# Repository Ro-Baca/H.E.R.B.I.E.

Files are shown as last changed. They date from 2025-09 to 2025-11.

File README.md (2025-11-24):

# **H.E.R.B.I.E.** <br> <span style="font-size:60%;">**H**orticultural **E**lectronic **R**obot **B**udy **I**nteractive **E**ntity</span>

> ![Logo de H.E.R.B.I.E. o la foto del robot]

 

H.E.R.B.I.E. es un prototipo de robot social de código abierto, diseñado para ser una plataforma de investigación accesible en el campo de la Interacción Humano-Robot (HRI). Fue desarrollado siguiendo una metodología de Ingeniería de Sistemas para estudiar cómo la filosofía de 'Robot Débil' puede fomentar la cooperación y el acoplamiento social con los usuarios.

## Modelo


### Conceptual
Define los **actores y requerimientos de usuario** (el "Qué" y "Por qué" del sistema). 

 

### Lógico
Describe la **estructura funcional** y las interacciones del sistema, agnósticas a la tecnología.

 

### Tecnológico
Define la **arquitectura concreta**, componentes de hardware y plataformas de software específicas.

 

## Hardware
Esta sección contiene los planos de los componentes y su interconexión, esenciales para la replicabilidad.
### Circuitos
Aquí se encuentran los diagramas eléctricos y pinouts para la interconexión de sensores y actuadores.

### CAD
Archivos STL para los encapsulamientos modulares, diseñados para impresión FDM en PLA.

## Software
El software se divide en una arquitectura dual:

### Cerebro (Raspberry Pi Zero)
-   **Función:** Procesamiento de alto nivel, servidor web y base de datos.
-   **Tecnologías:** Python, Flask, SQLite.

### Controlador (Raspberry Pi Pico)
-   **Función:** Gestión de entradas/salidas (lectura de sensores y control de actuadores) en tiempo real.
-   **Tecnologías:** MicroPython.

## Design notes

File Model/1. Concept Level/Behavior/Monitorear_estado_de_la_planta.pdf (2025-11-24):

uc [package] Behavior [Monitorear estado de la planta]

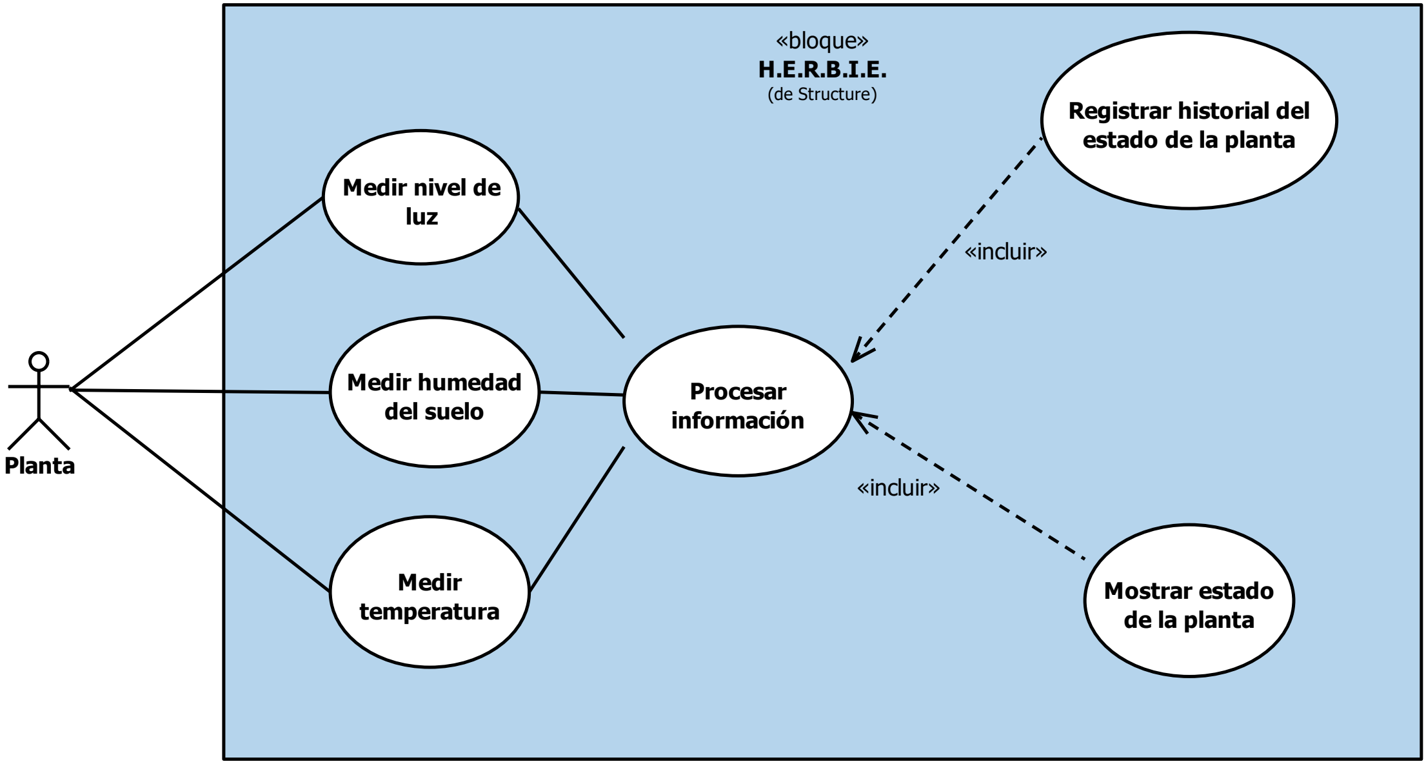
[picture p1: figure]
Planta; «bloque» H.E.R.B.I.E. (de Structure); Medir temperatura; Medir humedad del suelo; Medir nivel de luz; Procesar información; Mostrar estado de la planta; Registrar historial del estado de la planta; «incluir»

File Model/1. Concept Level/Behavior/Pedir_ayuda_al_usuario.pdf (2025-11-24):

uc [package] Behavior [Pedir ayuda al usuario]

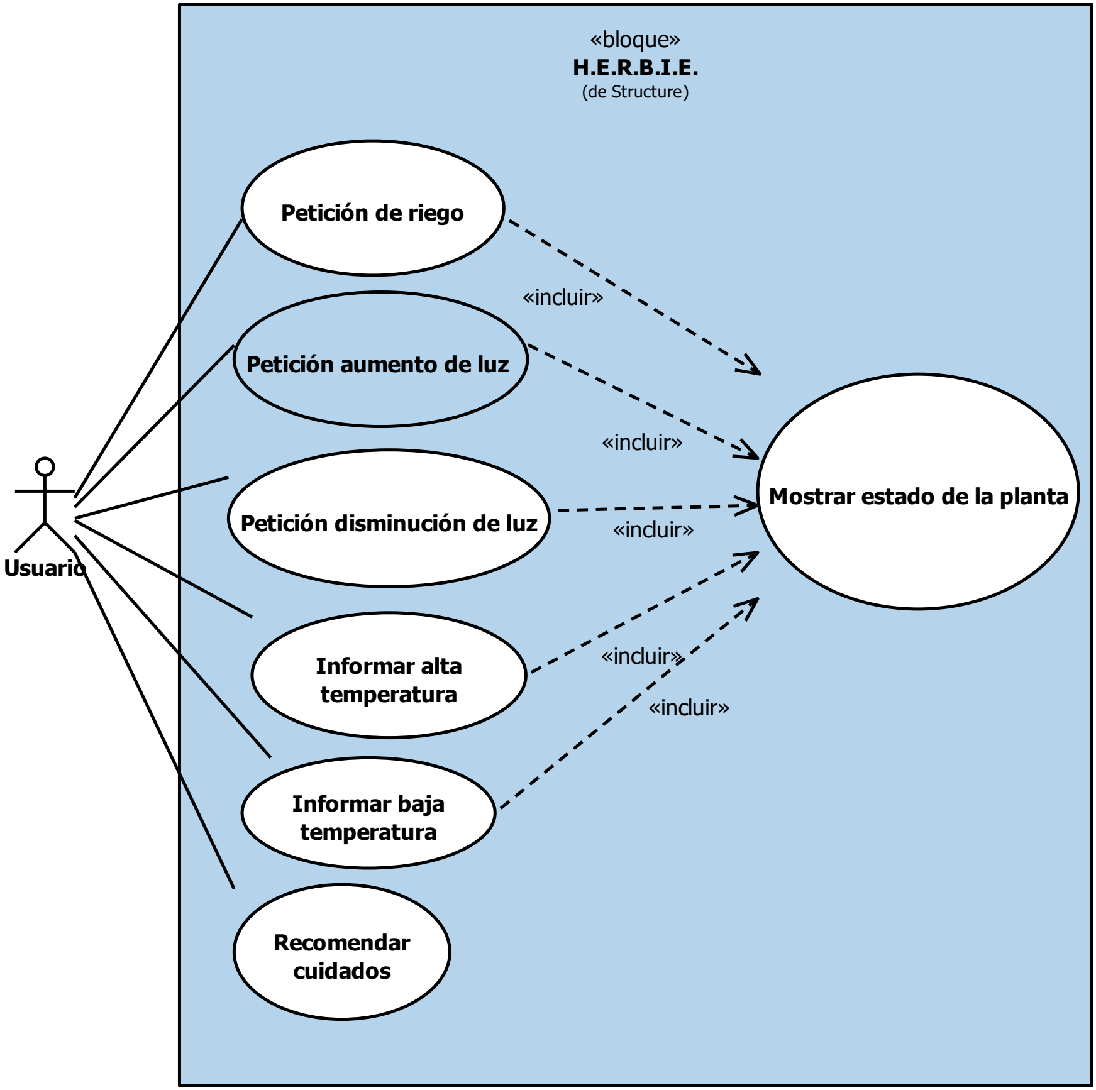
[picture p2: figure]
Usuario; «bloque» H.E.R.B.I.E. (de Structure); Petición aumento de luz; Petición de riego; Petición disminución de luz; Recomendar cuidados; Informar alta temperatura; Informar baja temperatura; Mostrar estado de la planta; «incluir»

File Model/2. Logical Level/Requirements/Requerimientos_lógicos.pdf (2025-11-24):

«requisito»
Sensor de temperatura
Id: LR-01
Text: El sistema debe de
contener un sensor capaz de medir la temperatura del
ambiente.

«requisito»
Sensor de humedad
Id: LR-02
Text: El sistema debe contener un sensor capaz de medir la humedad del suelo de la
planta.

«requisito»
Sensor de luz
Id: LR-03
Text: El sistema debe contener un sensor capaz de medir el nivel de luz que incide en la planta.

«requisito»
Controlador del sistema
Id: LR-04
Text: El sistema debe contener un elemento capaz de procesar la informacion de los sensores.

«requisito»
Sensado de temperatura
Id: LR-08
Text: El sistema deberá medir periódicamente la temperatura del ambiente utilizando el sensor de temperatura.

«requisito»
Sensado de humedad
Id: LR-09
Text: El sistema deberá medir periódicamente la humedad del suelo de la planta utilizando el sensor de humedad.

«requisito»
Sensado de nivel luz
Id: LR-10
Text: El sistema deberá medir periódicamente el nivel de luz que incide en la planta utilizando el sensor de luz.

«requisito»
Actuador de sonido
Id: LR-05
Text: El sistema debe contener un actuador para efectuar
acciones de sonido.

«requisito»
Actuador de luz
Id: LR-06
Text: El sistema debe contener un actuador para efectuar acciones de luz.

«requisito»
Interfaz de Usuario Gráfico Id: LR-07
Text: El sistema debe de
proveer una Interfaz Grafica de Usuario para interactuar con el usuario.

«requisito»
Base de datos Interna
Id: LR-13
Text: El sistema debe almacenar la informacion de los sensores localmente en una base de datos interna.

«requisito»
Señal de temperatura
Id: LR-20
Text: El sensor de temperatura debe mandar la señal de temperatura al controlador con el itemFlow Sens_data.

«requisito»
Señal de humedad
Id: LR-21
Text: El sensor de humedad debe mandar la señal de humedad al controlador con el itemFlow Sens_data.

«requisito»
Señal de luz
Id: LR-22
Text: El sensor de luz debe mandar la señal de nivel de luz con el itemFlow Sens_data.

«requisito»
Configuracion volumen del
actuador
Id: LR-16
Text: El sistema debe permitir al usuario configurar el volumen del actuador sonoro.

«requisito»
Configuración brillo del
actuador
Id: LR-17
Text: El sistema debe permitir al usuario configurar el brillo del actuador de luz.

«requisito»
Configuración frecuencia de medición
Id: LR-18
Text: El sistema debe de permitir al usuario configurar la frecuencia de medicion de los sensores.

«requisito»
Configuracion de umbral de Temperatura
Id: LR-11
Text: El sistema debe permitir al usuario configurar el valor de umbral de temperatura.

«requisito»
Configuración de umbral de humedad
Id: LR-15
Text: El sistema debe permitir al usuario configurar el valor de umbral de humedad.

«requisito»
Configuración de umral de nivel de luz
Id: LR-19
Text: El sistema debe permitir al usuario configurar el valor de umbral de nivel de luz.

«requisito»
Controlador de datos del
sensor
Id: LR-12
Text: El controllador debe recibir la información de los sensores para procesarla.

«requisito»
Mostrar información de planta Id: LR-14
Text: El controlador debe mandar la informacion del estado de la planta a la IUG.

«requisito»
Valores de configuracion del controlador.
Id: LR-23
Text: El controlador debe recibir el itemFlow config_values cuando un nuevo valor de configuracion es requerido.

«requisito»
Mostrar valores de
configuración
Id: LR-28
Text: La IUG debe mandar el itemFlow config_values al
controlador cuando se establece un nuevo valor.

«requisito»
Solicitud de actuación de
controlador
Id: LR-24
Text: El controlador debe mandar el itemFlow Act_com para solicitar una acción de los actuadores.

«requisito»
Función de procesamiento de sensor
Id: LR-26
Text: El controlador debe recibir el itemFlow sens_data, procesar la información y mandar la señal mes_values.

«requisito»
Función calcular estatus planta Id: LR-27
Text: El controlador debe recibír los intemFlow mes_values y
config_values para calcular el estado de la planta.

«requisito»
Mostrar informacion gráfica de planta
Id: LR-25
Text: La IGU debe recibír los intemFlow sens_data y plnt_stat para mostrar la información al usuario.

«requisito»
Función calcular emocion del robot Id: LR-29
Text: El controlador debe recibír el itemFlow plnt_stat para calcular la emoción del robot y mandar las señales son_com y lig_com.

«requisito»
Temperatura ok
Id: LR-31
Text: Cuando el itemFlow temp_sensor_data < max_temp y temp_sensor_data> min_temp, el controlador debe establecer temp_stat = ok.

«requisito»
Humedad ok
Id: LR-34
Text: Cuando el itemFlow moist_sensor_data < max_moist y moist_sensor_data > min_moist, el controlador debe establecer moist_stat = ok.

«requisito»
Luz ok
Id: LR-38
Text: Cuando light_sensor_data < max_light AND light_sensor_data > min_light, el controlador debe establacer temp_stat = ok.

«requisito»
Temperatura Alta
Id: LR-32
Text: Cuando el itemFlow temp_sensor_data >max_temp, el controlador debe establecer temp_stat = high.

«requisito»
Humedad alta
Id: LR-35
Text: Cuando moist_sensor_data > max_moist, el controlador debe establecer moist_stat = high.

«requisito»
Luz alta
Id: LR-39
Text: Cuando light_sensor_data > max_light, el controlador debe establecer light_stat = high.

«requisito»
Temperatura baja
Id: LR-33
Text: Cuando el itemFlow temp_sensor_data < min_temp, el controlador debe establecer temp_stat = low.

«requisito»
Humedad baja
Id: LR-36
Text: Cuando moist_sensor_data < min_moist, el controlador debe establecer moist_stat = low.

«requisito»
Luz baja
Id: LR-40
Text: Cuando light_sensor_data < max_light, el controlador debe establecer light_stat = low.

«requisito»
Estructura plnt_stat
Id: LR-30
Text: El itemFlow plnt_stat debe estar compuesto de tres variables: temp_stat, moist_stat y light_stat.

«requisito»
Estructura emocion del robot Id: LR-44
Text: El itemFlow robot_emo debe estar compuesto por tres variables: temp_emo, moist_emo, light_emo.

«requisito»
Emocion temperatura ok
Id: LR-45
Text: Cuando temp_stat == ok, el controlard debe establecer temp_emo = ok.

«requisito»
Emoción humedad ok
Id: LR-48
Text: Cuando moist_stat == ok, el controlador deber establecer moist_emo = ok.

«requisito»
Emoción luz ok
Id: LR-51
Text: Cuando light_stat == ok, el controlador deber establecer light_emo = ok.

«requisito»
Emoción temperatura caliente Id: LR-46
Text: Cuando temp_stat == high, el controlador debe establecer temp_emo = hot.

«requisito»
Emoción humedad seco
Id: LR-49
Text: Cuando moist_stat == low, el controlador deber establecer moist_emo = dry.

«requisito»
Sin humedad
Id: LR-37
Text: Cuando
moist_sensor_data == 0, el controlador debe establecer moist_stat = dead.

«requisito»
Emoción luz cansado
Id: LR-52
Text: Cuando light_stat == high, el controlador debe establecer light_emo = tired.

«requisito»
Emoción temperatura fría
Id: LR-47
Text: Cuando temp_stat == low, el controlador debe establecer temp_emo = cold.

«requisito»
Emoción humedad muerto
Id: LR-50
Text: Cuando moist_stat == dead, el controlador deber establecer moist_emo = dead.

«requisito»
Emoción luz triste
Id: LR-53
Text: Cuando light_stat == low, el controlador debe establecer light_emo = tired.

«requisito»
Comando emoción muesto
Id: LR-56
Text: Cuando mosit_emo == dead, el controlador debe establecer led_command = [red,still,fast] y sound_command = [0,0].

«requisito»
Estructura comando luz
Id: LR-54
Text: El itemFlow led_command debe estar compuesto de tres variables: color, modeo, velocidad.

«requisito»
Estructura comando sonido
Id: LR-55
Text: El itemFlow sound_command debe estar compuesto de dos variables: tono y velocidad.

«requisito»
Comando emoción seco
Id: LR-57
Text: Cuando mosit_emo == dry, el controlador debe establcer led_command = [blue,blink,fast] y sound_command = [1,-1].

«requisito»
Comando emoción frío
Id: LR-59
Text: Cuando temp_emo == cold y moist_emo == ok, el controlador debe establecer led_command = [blue,still,fast] y sound_command = [1,1].

«requisito»
Comando emoción triste
Id: LR-60
Text: Cuando light_emo == sad y temp_emo == ok y moist_emo == ok, el controlador debe establecer led_command = [blue,blink,slow] y sound_command = [-1,-1].

«requisito»
Comando emoción caliente
Id: LR-58
Text: Cuando temp_emo == hot y moist_emo == ok, el controlador debe establecer led_command = [red,blink,fast] y sound_command = [1,1].

«requisito»
Comando emoción cansado
Id: LR-61
Text: Cuando light_emo == tired y temp_emo == ok y moist_emo == ok, el controlador debe establecer led_command = [green,blink,fast] y sound_command = [-1,-1].

«requisito»
Comando emoción feliz
Id: LR-62
Text: Cuando light_emo == ok y temp_emo == ok y moist_emo == ok, el controlador debe establecer led_command = [green,still,fast] y sound_command = [0,0].
Estructura | Funcionalidad
DataFlow | Estado de la planta

Emociones
del robot

Comandos
de actuación

«requisito»
Estados principales del sistema Id: LR-41
Text: El sistema debe tener dos estados principales "encendido" y "apagado".

«requisito»
Estado "encendido"
Id: LR-42
Text: Mientras el sistema este en el estado "encendido" debe entrar en los estados "monitorear planta", "Monitorear plantas" y "Determinar emcion del robot".

«requisito»
System Actuate emotion state Id: LR-43
Text:
Cuando plnt_emo != ok, el sistema debe entrar en el estado "Actuar emocion".

Estados del
robot

req [package] Requirements [Requerimientos lógicos]

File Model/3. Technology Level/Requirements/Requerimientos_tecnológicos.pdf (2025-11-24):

«requisito»
Controlador principal
Id: TR-01
Text: El sistema utilizará un microprocesador Raspberry Pi Zero como unidad de control principal para tareas de alto nivel.

«requisito»
Microcontrolador de Entradas y Salidas
Id: TR-02
Text: El sistema debe usar un microcontrolador Raspberry Pi Pico para la gestión de entradas y salidas

«requisito»
Comuncacion de control
Id: TR-04
Text: La comunicación entre la Pi Zero y la Pi Pico debe
implementarse usando el
protocolo serial UART

«requisito»
Firmware del
microcontrolador
Id: TR-05
Text: El firmware de la Raspberry Pi Pico debe ser desarrollado en MicroPython

«requisito»
Servidor Web de Interfaz
Id: TR-06
Text: La GUI debe ser servida por un servidor web local
implementado con el micro-framework Flask

«requisito»
Almacenamiento Base de Datos Id: TR-07
Text: El historial de datos de los sensores debe almacenarse en una base de datos local SQLite

«requisito»
Sensor de Temperatura
Id: TR-08
Text: El sistema debe usar un sensor DHT11 para medir la temperatura ambiental.

«requisito»
Sensor de luz
Id: TR-09
Text: El sistema debe usar un sensor BH1750 para medir la intensidad de luz ambiental.

«requisito»
Sensor de humedad
Id: TR-10
Text: El sistema debe usar un sensor capacitivo OKY3443-1 para medir la humedad del
suelo.

«requisito»
Actuador Visual
Id: TR-11
Text: El sistema debe usar una tira de LEDs direccionables WS2812B para la retroalimentación visual.

«requisito»
Actuador Auditivo
Id: TR-12
Text: El sistema debe usar un Buzzer Pasivo controlado por PWM para la retroalimentación auditiva.

«requisito»
Fabricacion de la carcaza
Id: TR-13
Text: La carcaza y los
encapsulamientos internos deben ser fabricados mediante Impresión 3D.

«requisito»
Material de fabricacion
Id: TR-14
Text: El material de
fabricacion debe ser Ácido Poliláctico (PLA).

«requisito»
Plataforma CAD
Id: TR-15
Text: El diseño de la carcaza debe ser modelado en la plataforma
"Onshape" y ser de acceso público

«requisito»
Fuente de alimentacion
Id: TR-16
Text: El sistema debe ser
alimentado por una única fuente de alimentación centralizada de 5 Volts y 2 Ampers.

«requisito»
Frequencia de muestreo
Id: TR-17
Text: El microcontrolador debe leer todos los sensores físicos con una frecuencia de 1 Segundo.

«requisito»
Filtrado de señal
Id: TR-19
Text: El sistema debe permitir la configuración de la cantidad de mediciones a promediar.

«requisito»
Filtrado de media movil
Id: TR-18
Text: el sistema debe promediar los valores recibidos por los sensores y promediarlos despues de una cantidad especifica de mediciones antes de reportar el valor final.

«requisito»
Estructura GUI
Id: TR-20
Text: La Interfaz Gráfica de Usuario debe estar estructurada en cuatro pantallas principales: Inicio, Estadísticas, Consejos y Configuración.

«requisito»
Refresco de datos de GUI
Id: TR-27
Text: Los datos de los sensores mostrados en la pantalla "Inicio" deben refrescarse automáticamente cada 3 segundos.

«requisito»
Plantilla de GUI
Id: TR-21
Text: La Interfaz Grafica de usuario debe usar una plamntilla para compartir la estructura entre pantallas.

«requisito»
Estructura de Plantilla
Id: TR-22
Text: La estructura de la plantilla debe estar compuesta de botones para navegar por la interfaz, el nombre del robot y la pagina actual.

«requisito»
Pantalla de inicio
Id: TR-23
Text: La pantalla de inicio debe de mostrar las mediciones actuales de los sensores, la estampa de tiempo de la ultima medicion, el estado actual del robot y el perfil seleccionado actualmente.

«requisito»
Pantalla de Consejos
Id: TR-25
Text: La pantalla de consejos debe de presentar informacion relevante para el cuidado del perfil de planta seleccionado.

«requisito»
Pantalla de estadisticas
Id: TR-24
Text: La pantalla de estaisticas debe mostrar el registro de mediciones del robot para cada sensor.

«requisito»
Pantalla de configuracion
Id: TR-26
Text: La pantalla de configuracion debe mostrar un menu que permita al usuario cambiar las configuraciones del robot.

«requisito»
Configuracion de actuadores Id: TR-28
Text: La pantalla de configuracion debe permitir al usuario configurar la intesisdad de los actuadores de volumen y brillo.

«requisito»
Voltajes de operacion
Id: TR-03
Text: Los componentes del
sistema deben operar a 5V y 3.3V

req [package] Requirements [Requerimientos tecnológicos]

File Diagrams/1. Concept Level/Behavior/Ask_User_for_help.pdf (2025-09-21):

uc [package] Behavior [Ask User for help]

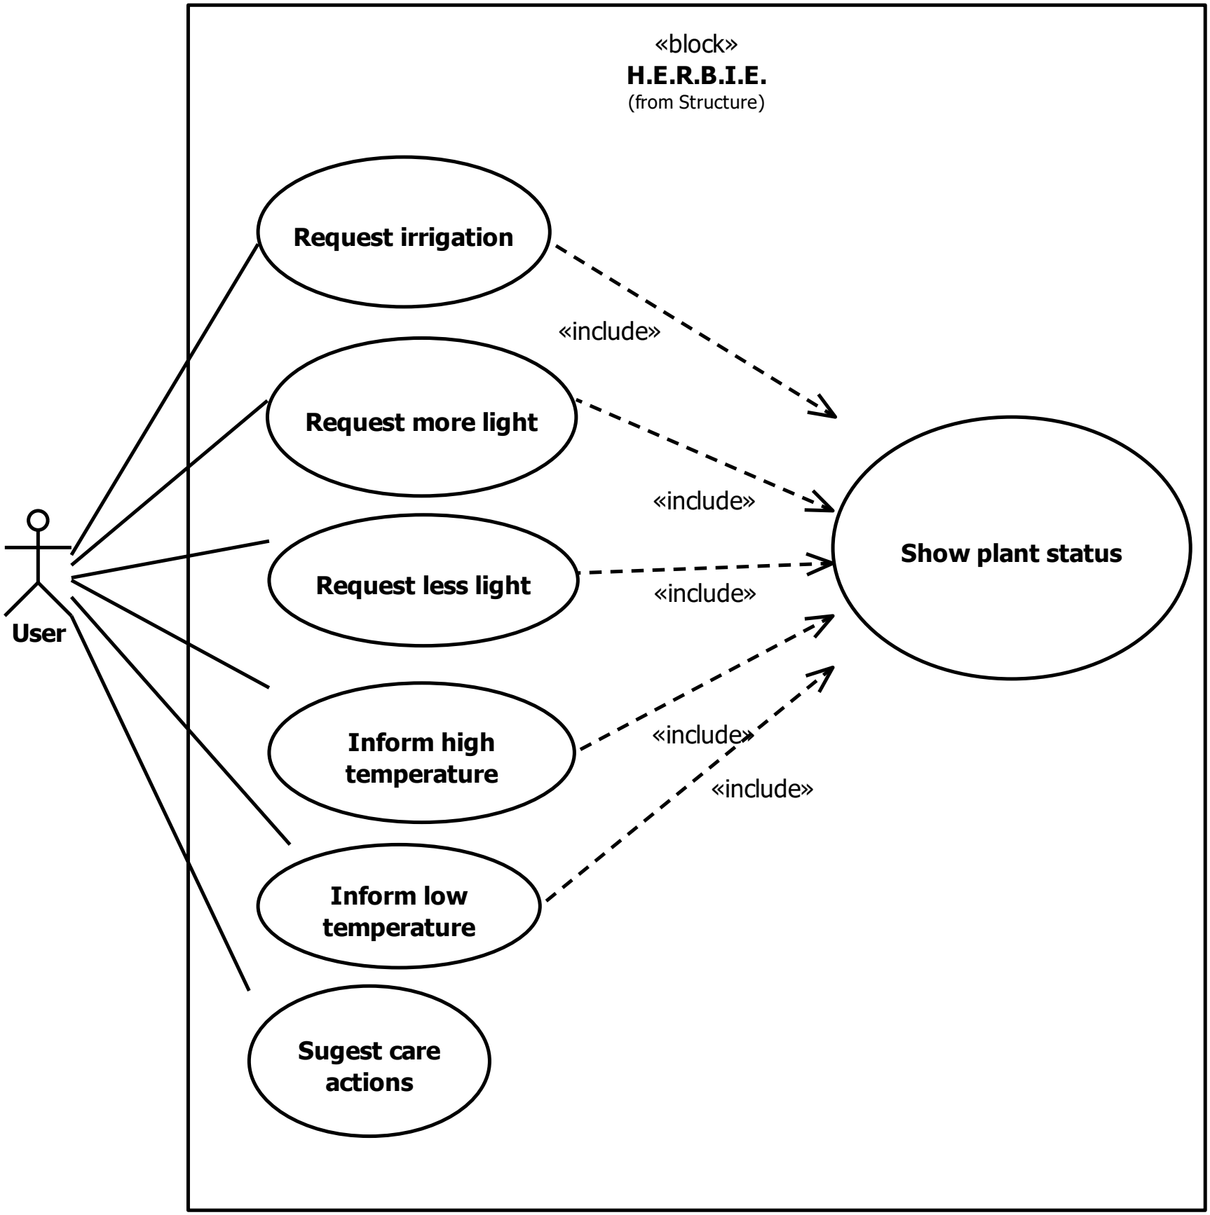
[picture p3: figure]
User; «block» H.E.R.B.I.E. (from Structure); Request more light; Request irrigation; Request less light; Sugest care actions; Inform high temperature; Inform low temperature; Show plant status; «include»

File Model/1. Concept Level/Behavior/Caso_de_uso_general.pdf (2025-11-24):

uc Caso de uso general

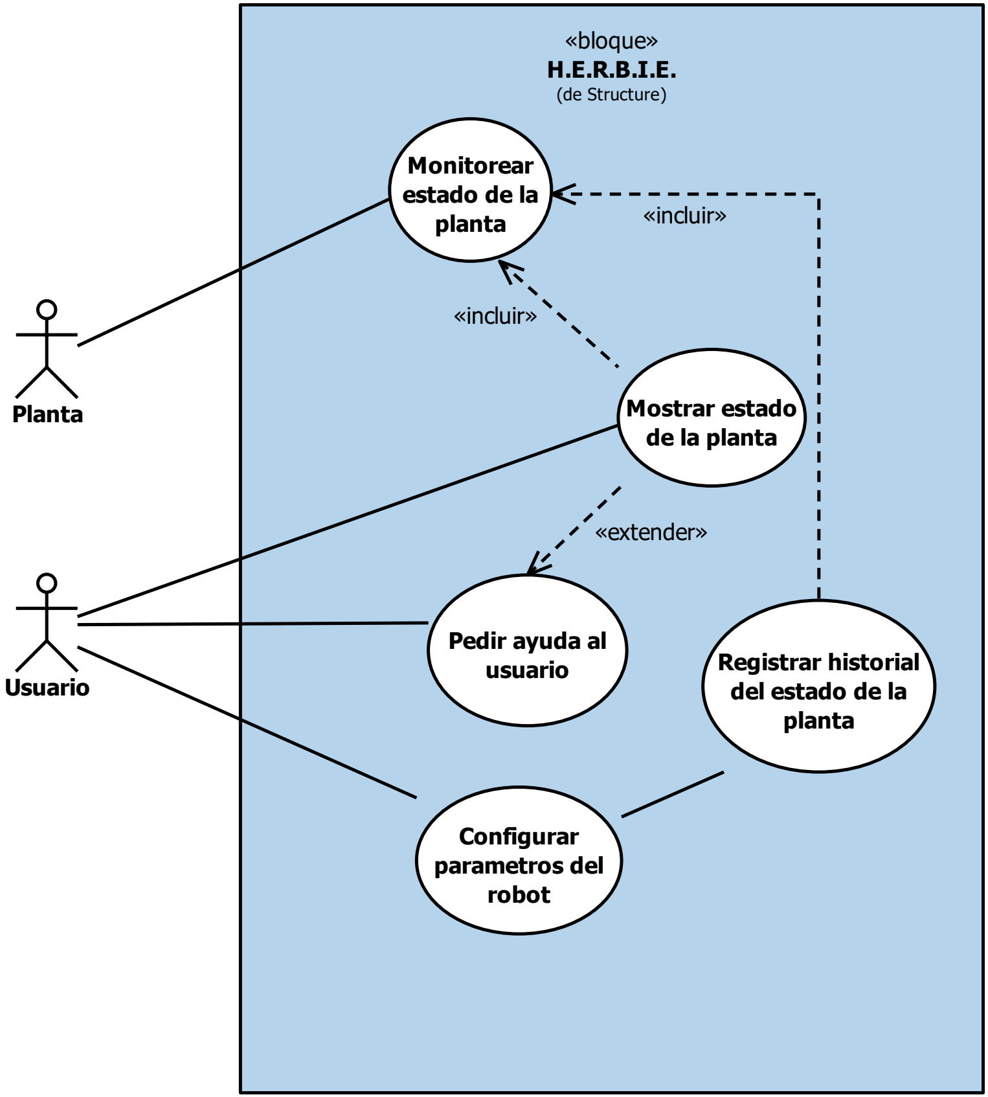
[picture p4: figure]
«bloque» H.E.R.B.I.E. (de Structure); Configurar parametros del robot; Registrar historial del estado de la planta; Mostrar estado de la planta; Pedir ayuda al usuario; Monitorear estado de la planta; Usuario; Planta; «incluir»; «extender»

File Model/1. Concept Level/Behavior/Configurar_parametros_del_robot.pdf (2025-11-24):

uc [package] Behavior [Configurar parametros del robot]

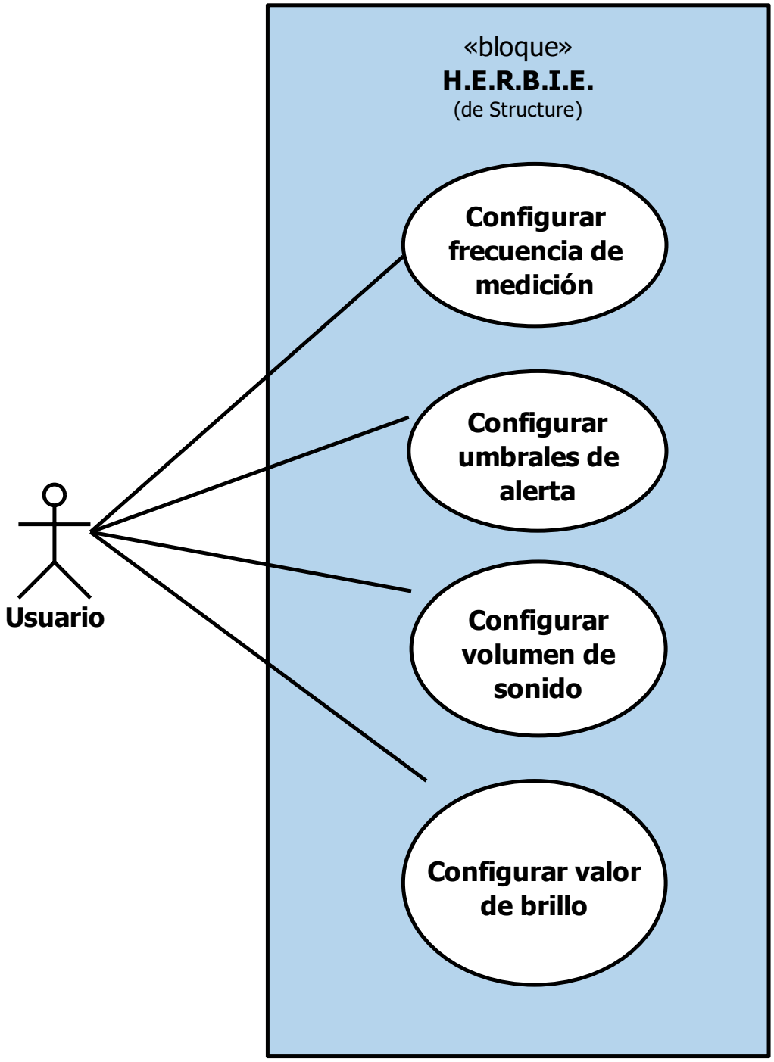
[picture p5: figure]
«bloque» H.E.R.B.I.E. (de Structure); Configurar frecuencia de medición; Configurar umbrales de alerta; Configurar volumen de sonido; Configurar valor de brillo; Usuario

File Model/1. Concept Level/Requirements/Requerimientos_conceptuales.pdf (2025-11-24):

«requisito»
Monitoreo del ambiente
Id: CR-01
Text: El sistema debe ser
capaz de medir variables del ambiente.

«requisito»
Umbrales criticos
Id: CR-06
Text: El sistema debe comparar los valores medidos del ambiente contra los valores de umbral preconfigurados.

«requisito»
Sensado de Temperatura
Id: CR-02
Text: El sistema debe ser
capaz de medir la
temperatura del ambiente

«requisito»
Sensado de nivel de luz
Id: CR-03
Text: El sistema debe ser
capaz de medir el nivel de luz que incide en la planta.

«requisito»
Sensado de humedad
Id: CR-04
Text: El sistema debe ser
capaz de medir la humedad
en el suelo de la planta.

«requisito»
Generación de alerta sonora Id: CR-08
Text: El sistema debe ser capaz de generar una alerta sonora cuando sea necesario.

«requisito»
Generación de alerta visual Id: CR-09
Text: El sistema debe ser capaz de generar una alerta visual cuando sea necesario.

«requisito»
Control de volumen
Id: CR-18
Text: El sistema debe permitir al usuario configurar el volumen del sonido del sistema.

«requisito»
Control de brillo
Id: CR-19
Text: El sistema debe permitir al usuario configurar el valor de brillo del sistema

«requisito»
Control de frecuencia de
medición
Id: CR-20
Text: El sistema debe permitir al usuario configurar la frecuencia de medicion del sistema.

«requisito»
Base de datos local
Id: CR-22
Text: El sistema debe de proveer una base de datos local para registrar los valores medidos.

«requisito»
Operación off-line
Id: CR-25
Text: El sistema debe ser capaz de operar sus funciones esenciales sin una conección a internet.

«requisito»
Funciones escenciales
Id: CR-26
Text: El sistema debe entender como funciones esenciales: sensado de temperatura, sensado de nivel de luz, sensado de humedad, generación de alerta sonora y generación de alerta visual.

«requisito»
Menu de configuración
Id: CR-17
Text: El sistema debe proveer al usuario un menu para asignar los valores de configuración.

«requisito»
Control umbrales de
medición
Id: CR-21
Text: El sistema debe permitir al usuario configurar los valores de umbral.

«requisito»
Presentación de emociones
Id: CR-27
Text: El sistema debe ser capaz de simular emociones utilizando señales de luz y sonido.

«requisito»
Mantenimiento facil
Id: CR-28
Text: Los componentes del
sistema deben ser accesibles para su facil mantenimiento.

«requisito»
Restricción de datos
Id: CR-23
Text: El sistema no debe de recolectar información sensible ni personal del usuario sin su concentimiento.

«requisito»
Protección de información
Id: CR-24
Text: El sistema no debe compartir informacion recolectada sin permiso del usuario.

«requisito»
Estado de la planta
Id: CR-10
Text: El sistema debe proveer al usuario una interfaz para visualizar el estado de la planta

«requisito»
Procesamiento de información Id: CR-05
Text: El sistema debe ser capaz de procesar la informacion recollectada del ambiente.

«requisito»
Pedir ayuda
Id: CR-07
Text: El sistema debe ser capaz de generar alertas cuando un
parametro medido esta fuera de los rangos deseados.

«requisito»
Solicitud de riego
Id: CR-11
Text: El sistema debe ser capaz de solicitar al usuario regar la planta cuando la humedad de la tierra en la planta es inferior al valor de umbral configurado.

«requisito»
Solicitud incremento de luz Id: CR-12
Text: El sistema debe ser capaz de solicitar al usuario incrementar el nivel de luz cuando el valor de nivel de luz en la planta es menor al valor de umbral configurado.

«requisito»
Solicitud reduccion de luz Id: CR-13
Text: El sistema debe ser capaz de solicitar al usuario reducir el nivel de luz cuando el valor de nivel de luz en la planta es mayor al valor de umbral configurado.

«requisito»
Informacion de alta temperatura Id: CR-15
Text: El sistema debe ser capaz de informar al usuaio cuando la temperatura del ambientes es mayor al valor de umbral configurado

«requisito»
Informacion de baja temperatura Id: CR-14
Text: El sistema debe ser capaz de informar al usuaio cuando la temperatura del ambientes es menor al valor de umbral configurado

«requisito»
Recomendaciones de cuidado Id: CR-16
Text: El sistema debe ser capaz de proveer recomendaciones de cuidado al usuario.

«requisito»
Emociones del robot
Id: CR-29
Text: El sistema debe expresar seis emociones diferentes: muerto, seco, acalorado, frio, triste, cansado y feliz.

req [package] Requirements [Requerimientos conceptuales]

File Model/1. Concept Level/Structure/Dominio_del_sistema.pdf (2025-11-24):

bdd [package] Structure [Dominio del sistema]

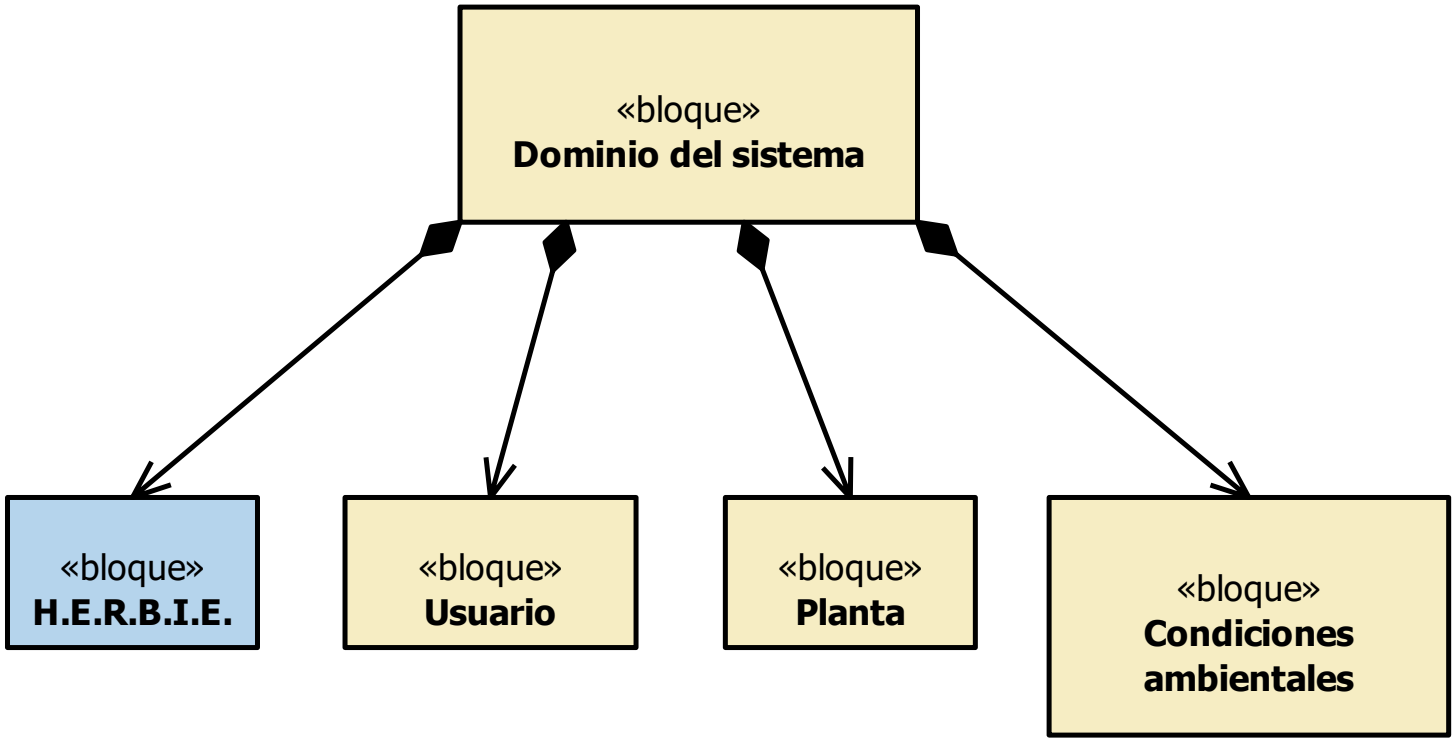
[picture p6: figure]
«bloque» Dominio del sistema; «bloque» H.E.R.B.I.E.; «bloque» Usuario; «bloque»; Planta; Condiciones ambientales

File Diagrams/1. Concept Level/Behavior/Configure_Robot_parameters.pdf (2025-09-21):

uc [package] Behavior [Configure Robot parameters]

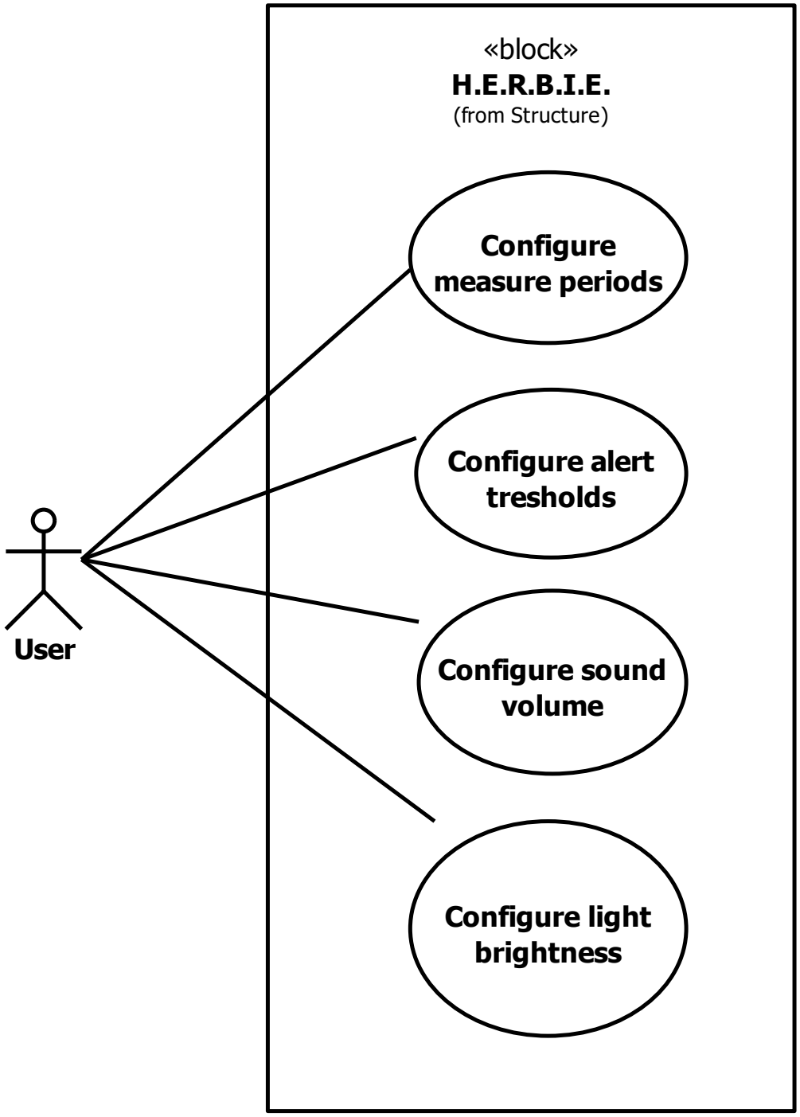
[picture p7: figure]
«block» H.E.R.B.I.E. (from Structure); Configure measure periods; Configure alert tresholds; Configure sound volume; Configure light brightness; User

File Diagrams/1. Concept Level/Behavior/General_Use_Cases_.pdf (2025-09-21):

uc General Use Cases

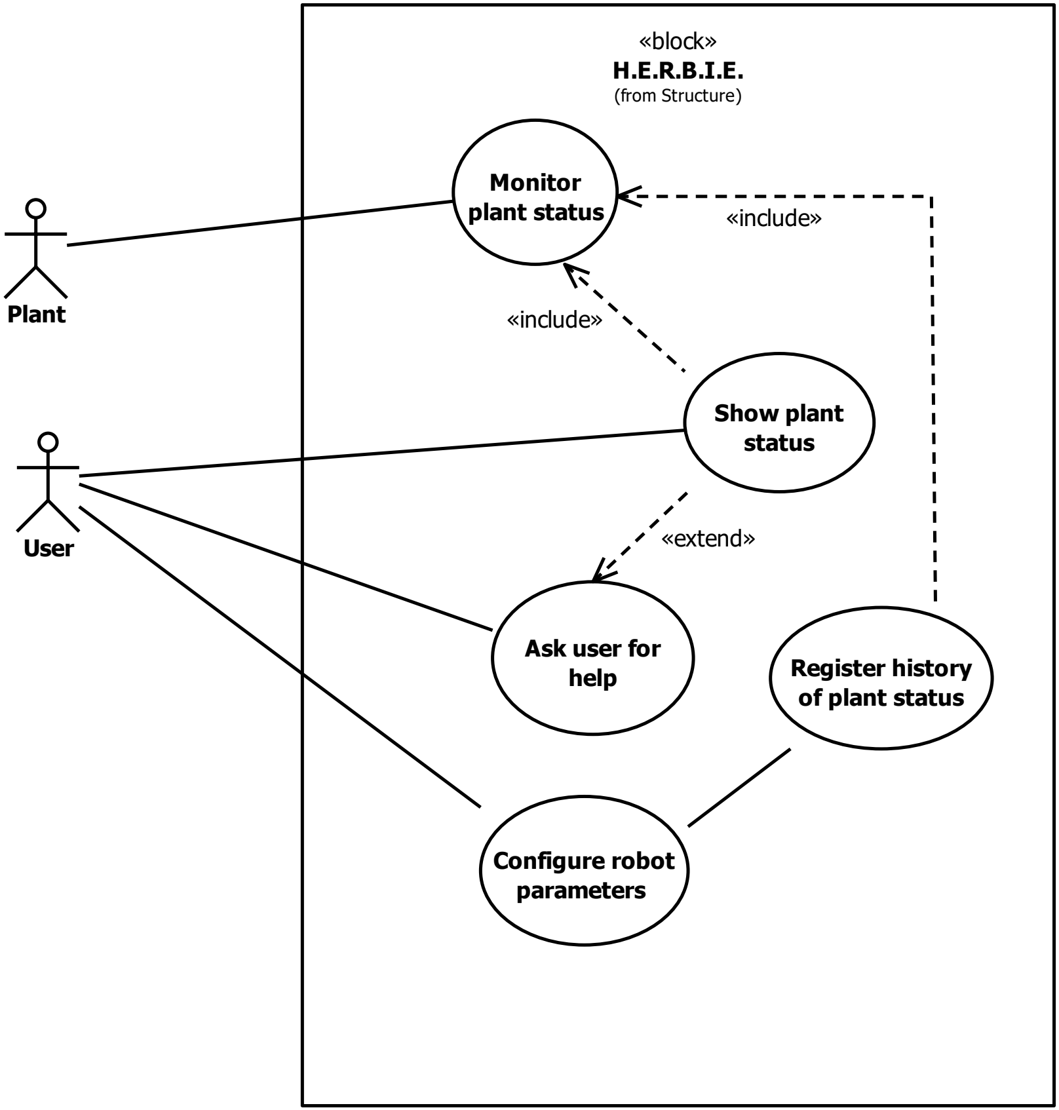
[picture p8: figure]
«block» H.E.R.B.I.E. (from Structure); Configure robot parameters; Register history of plant status; Show plant status; Ask user for help; Monitor plant status; User; Plant; «include»; «extend»

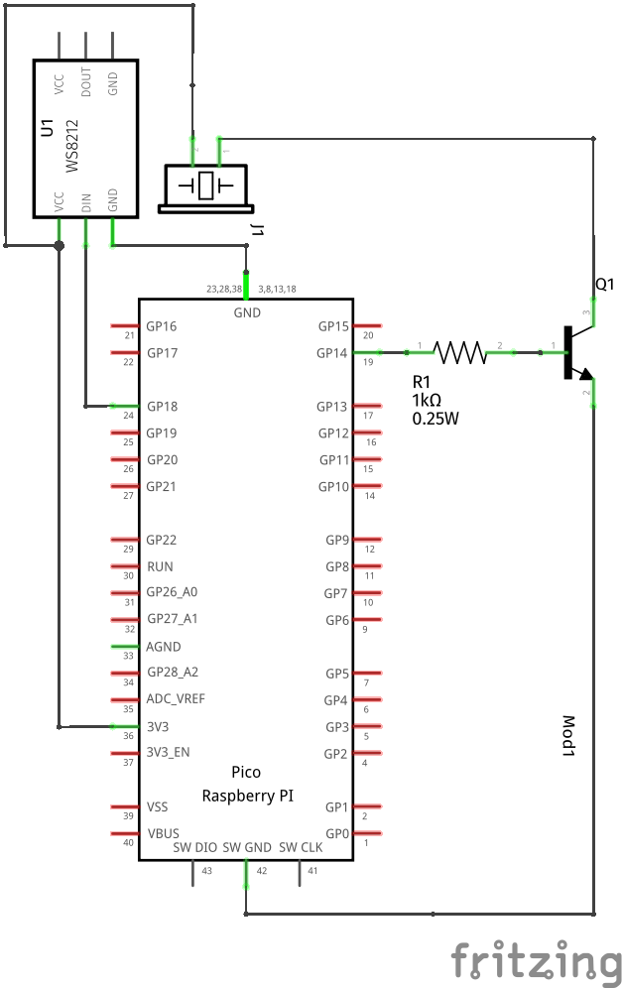
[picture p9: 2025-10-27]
docs/Images/Circuits/ActuatorsSch.png

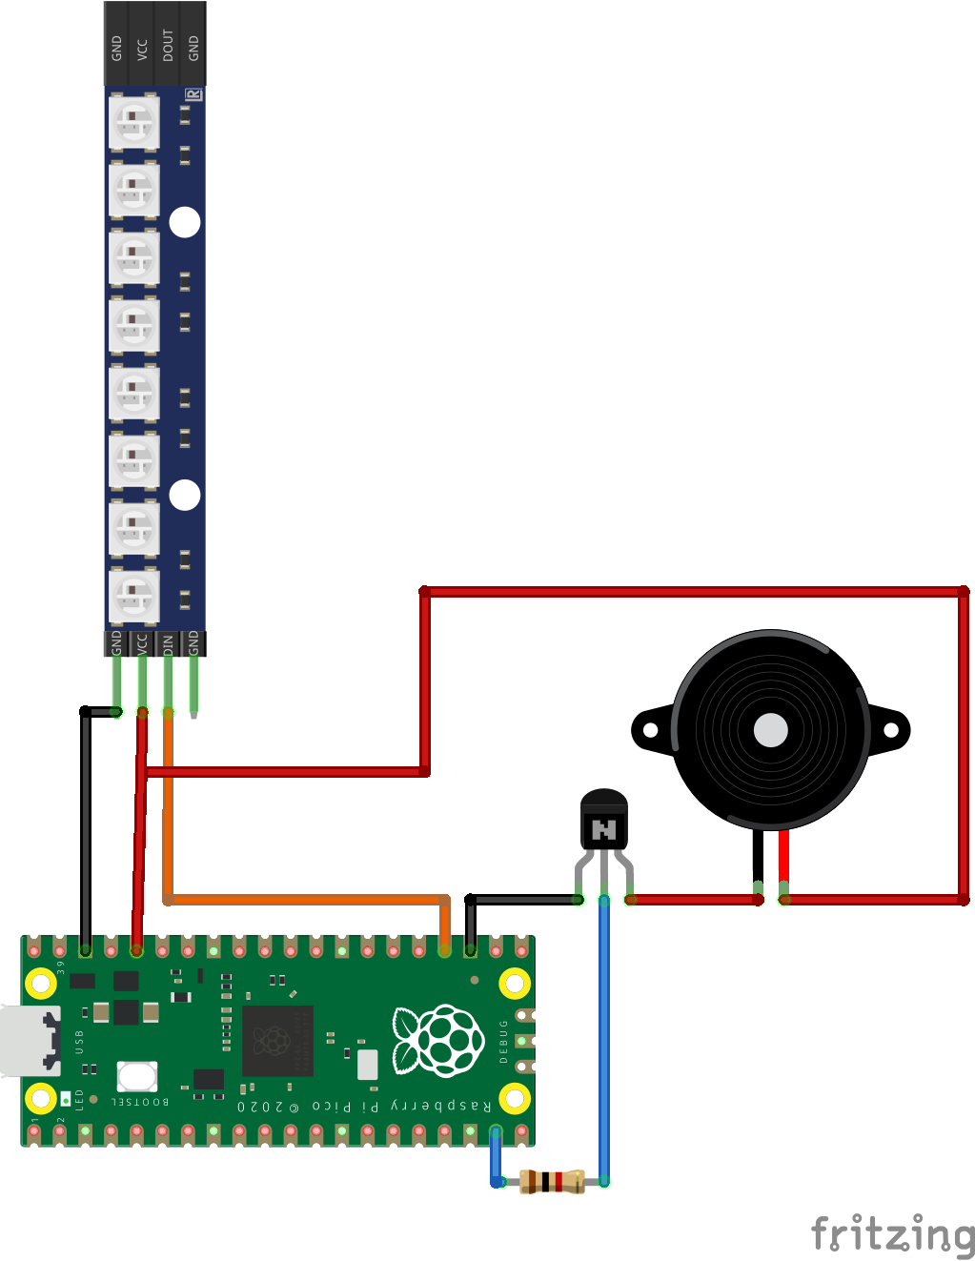
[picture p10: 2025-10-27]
docs/Images/Circuits/Actuators.png

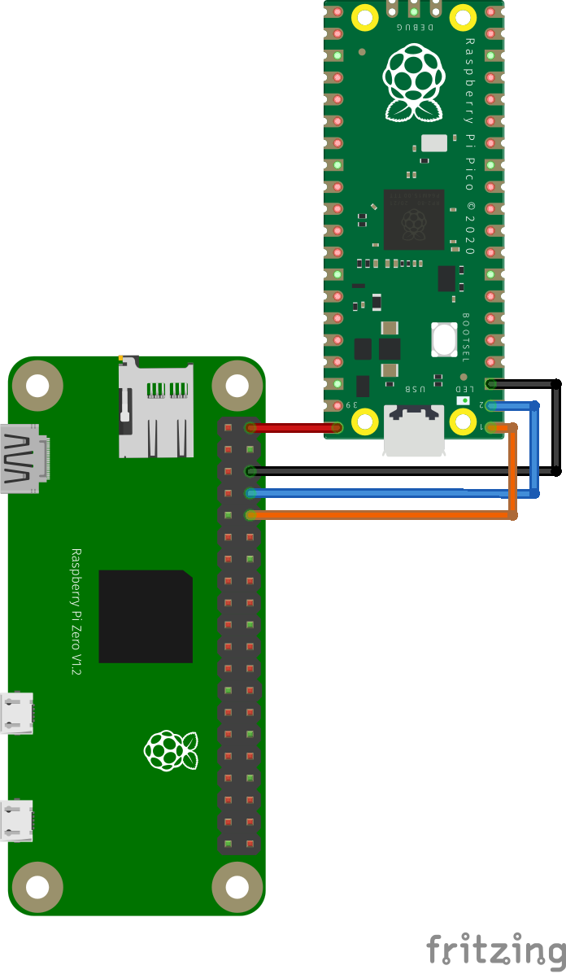
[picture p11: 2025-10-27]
docs/Images/Circuits/Control.png

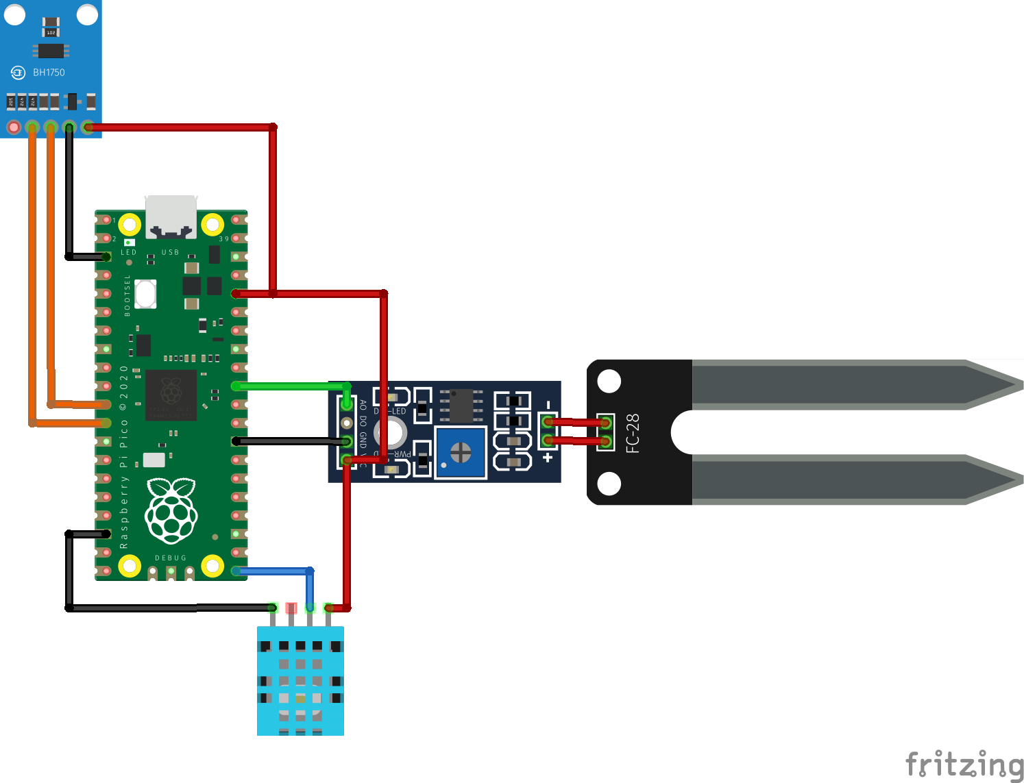
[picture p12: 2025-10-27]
docs/Images/Circuits/Sensors.png

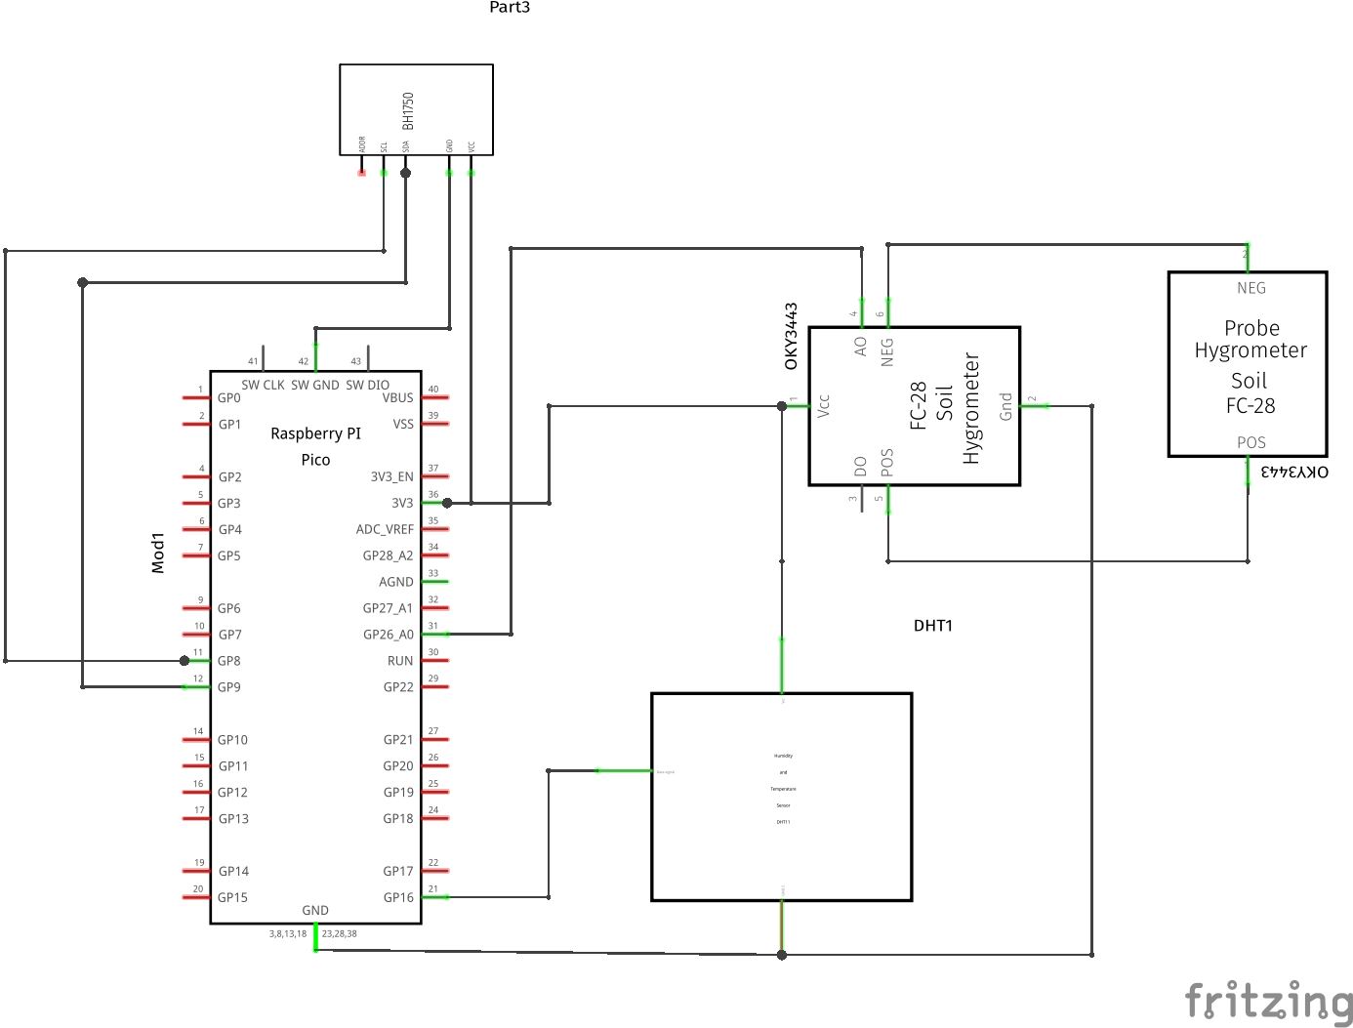
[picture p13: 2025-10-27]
docs/Images/Circuits/SensorSch.png

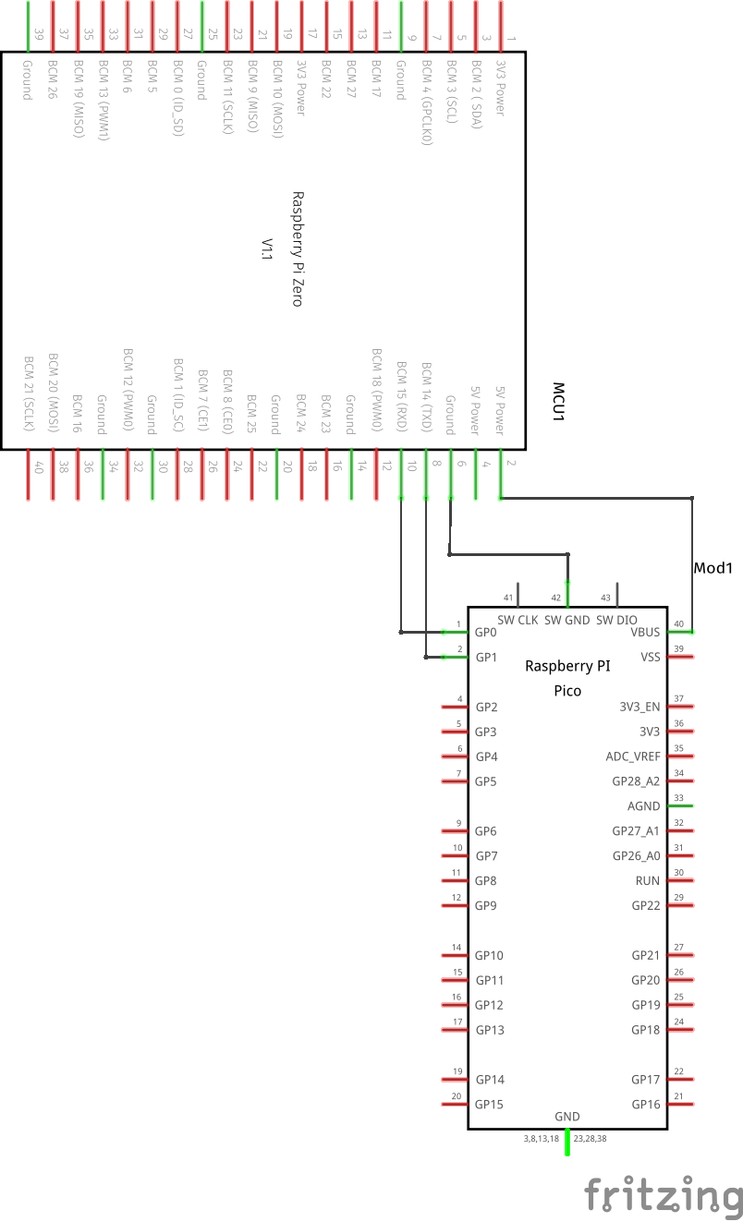
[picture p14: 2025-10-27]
docs/Images/Circuits/ControlSch.png

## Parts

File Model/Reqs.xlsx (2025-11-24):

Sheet: Reqs
ID | Nombre | Texto | Nivel de abstracción | Satisfy | Concepto
CR-01 | Monitoreo del ambiente | El sistema debe ser capaz de medir variables del ambiente. | Conceptual | LR-01, LR-02, LR-03, TR-08, TR-09, TR10 | Sensores y procesamiento
CR-02 | Sensado de Temperatura | El sistema debe ser capaz de medir la temperatura del ambiente | Conceptual | LR-01, LR-08, LR-31, LR-32, LR-33, TR-08 | Sensores y procesamiento
CR-03 | Sensado de nivel de luz | El sistema debe ser capaz de medir el nivel de luz que incide en la planta. | Conceptual | LR-03, LR-10, LR-38, LR-39, LR-40, TR-09, TR-31 | Sensores y procesamiento
CR-04 | Sensado de humedad | El sistema debe ser capaz de medir la humedad en el suelo de la planta. | Conceptual | LR-02, LR-09, LR-34, LR-35, LR-36, TR.10, TR-32 | Sensores y procesamiento
CR-05 | Procesamiento de información | El sistema debe ser capaz de procesar la informacion recollectada del ambiente. | Conceptual | LR-04, LR-12, LR-26, LR27, TR-01, TR-02, TR-29 | Sensores y procesamiento
CR-06 | Umbrales criticos | El sistema debe comparar los valores medidos del ambierite contra los valores de umbral preconfigurados | Conceptual | LR-27, LR-31, LR-40 | Sensores y procesamiento
CR-07 | Pedir ayuda | El sistema debe ser capaz de generar alertas cuando un parametro medido esta fuera de los rangos deseados. | Conceptual | LR-29, LR-47 a LR-53, LR-56 a 62, TR-11, TR-12 | Alertas y actuadores
CR-08 | Generación de alerta sonora | El sistema debe ser capaz de generar una alerta sonora cuando sea necesario. | Conceptual | LR-05, LR-55, TR-12 | Alertas y actuadores
CR-09 | Generación de alerta visual | El sistema debe ser capaz de generar una alerta visual cuando sea necesario. | Conceptual | LR-06, LR54, TR-11 | Alertas y actuadores
CR-10 | Estado de la planta | El sistema debe proveer al usuario una interfaz para visualizar el estado de la planta | Conceptual | LR-07, LR-29, TR-06, TR-20, TR-23, TR-30 | GUI y config
CR-11 | Solicitud de riego | El sistema debe ser capaz de solicitar al usuario regar la planta cuando la humedad de la tierra en la planta es inferior al valor de umbral configurado. | Conceptual | LR-49, a LR-57 | Alertas y actuadores
CR-12 | Solicitud incremento de luz | El sistema debe ser capaz de solicitar al usuario incrementar el nivel de luz cuando el valor de nivel de luz en la planta es menor al valor de umbral configurado. | Conceptual | LR-53 a LR-60 | Alertas y actuadores
CR-13 | Solicitud reduccion de luz | El sistema debe ser capaz de solicitar al usuario reducir el nivel de luz cuando el valor de nivel de luz en la planta es mayor al valor de umbral configurado. | Conceptual | LR-52 a LR61 | Alertas y actuadores
CR-14 | Informacion de baja temperatura | El sistema debe ser capaz de informar al usuaio cuando la temperatura del ambientes es menor al valor de umbral configurado | Conceptual | LR-47 a LR-59 | Alertas y actuadores
CR-15 | Informacion de alta temperatura | El sistema debe ser capaz de informar al usuaio cuando la temperatura del ambientes es mayor al valor de umbral configurado | Conceptual | LR-46 a LR-58 | Alertas y actuadores
CR-16 | Recomendaciones de cuidado | El sistema debe ser capaz de proveer recomendaciones de cuidado al usuario. | Conceptual | LR-66, TR-25 | GUI y config
CR-17 | Menu de configuración | El sistema debe proveer al usuario un menu para asignar los valones de configuración. | Conceptual | LR-28, TR-26 | GUI y config
CR-18 | Control de volumen | El sistema debe permitir al usuario configurar el volumen del sonido del sistema. | Conceptual | LR-16, TR-28 | GUI y config
CR-19 | Control de brillo | El sistema debe permitir al usuario configurar el valor de brillo del sistema | Conceptual | LR-17, TR-28 | GUI y config
CR-20 | Control de frecuencia de medición | El sistema debe permitir al usuario configurar la frecuencia de medicion del sistema. | Conceptual | LR-18, TR-19 | GUI y config
CR-21 | Control umbrales de medición | El sistema debe permitir al usuario configurar el perfil de planta a cuidar. | Conceptual | LR-11, LR-15, LR-19, TR-26 | GUI y config
CR-22 | Base de datos local | El sistema debe de proveer una base de datos local para registrar los valores medidos. | Conceptual | LR-12, TR-07, TR-24, TR-34 | GUI y config
CR-23 | Restricción de datos | El sistema no debe de recolectar información sensible ni personal del usuario sin su concentimiento.. | Conceptual | TR-07, TR-06 | No Funcionales
CR-24 | Protección de información | El sistema no debe compartir informacion recolectada sin permiso del usuario. | Conceptual | TR-07, TR-06 | No Funcionales
CR-25 | Operación Off-line | El sistema debe ser capaz de operar sus funciones esenciales sin una conección. a internet. | Conceptual | TR-33 | No Funcionales
CR-26 | Funciones escenciales | El sistema debe entender como funciones esenciales: sensado de temperatura, sensado de nivel de luz, sensado de humedad, generación de alerta sonora y generación de alerta visual. | Conceptual | TR-33 | No Funcionales
CR-27 | Presentación de emociones | El sistema debe ser capaz de comunicar el estado de la planta utilizando señales de luz y sonido. | Conceptual | LR-29, LR-47 a LR-53, LR-56 a 62, TR-11, TR-12 | Alertas y actuadores
CR-28 | Mantenimiento facil | Los componentes del sistema deben ser accesibles para su facil mantenimiento. | Conceptual | TR-13, TR-15 | No Funcionales
CR-29 | Emociones del robot | El sistema debe expresar ocho emociones diferentes: muerto, seco, acalorado, frio, triste, cansado feliz y advertencia. | Conceptual | LR-29, LR-47 a LR-53, LR-56 a 62, TR-11, TR-12 | Alertas y actuadores
CR-30 | Emocion Muerto | El sistema debe expresas la emocion muerte con un color rojo y sin hacer sonido | Conceptual | LR-56, TR-11 | Alertas y actuadores
CR-31 | Emocion Seco | El sistema debe expresas la emocion seco con un color amarillo y un sonido de alarma | Conceptual | LR-57, TR-11, TR-12 | Alertas y actuadores
CR-32 | Emocion Acalorado | El sistema debe expresas la emocion acalorado con un color rojo alternante y un sonido agudo | Conceptual | LR-58, TR-11, TR-12 | Alertas y actuadores
CR-33 | Emocion Frio | El sistema debe expresas la emocion frio con un color azul alternante y un sonido que asemeje un templor de frio | Conceptual | LR-59, TR-11, TR-12 | Alertas y actuadores
CR-34 | Emocion Triste | El sistema debe expresas la emocion trsite con un color magenta y un sonido que asemeje un lamento | Conceptual | LR-60, TR-11, TR-12 | Alertas y actuadores
CR-35 | Emocion Cansado | El sistema debe expresas la emocion cansado con un color cian y un sonido que asemeje una expresion de nervios | Conceptual | LR-61, TR-11, TR-12 | Alertas y actuadores
CR-36 | Emocion Feliz | El sistema debe expresas la emocion feliz con un color verde y sin hacer sonido | Conceptual | LR-62, TR-11 | Alertas y actuadores
CR-37 | Emocion Advertencia | El sistema debe expresas la emocion advertencia con un color naranja y sin hacer sonido | Conceptual | LR-63, LR-64, LR-65, TR-11 | Alertas y actuadores
CR-38 | Gestión de Perfiles de Planta | El sistema debe permitir al usuario seleccionar entre perfiles de planta predefinidos, la selección de un perfil debe ajustar automáticamente los umbrales de medición. | Conceptual | CR-21, LR-14, LR-15, LR-19, LR-66, TR-26 | GUI y config
LR-01 | Sensor de temperatura | El sistema debe de contener un sensor capaz de medir la temperatura del ambiente. | Lógico | TR-08 | Sensores y procesamiento
LR-02 | Sensor de humedad | El sistema debe contener un sensor capaz de medir la humedad del suelo de la planta. | Lógico | TR-10, TR-32 | Sensores y procesamiento
LR-03 | Sensor de luz | El sistema debe contener un sensor capaz de medir el nivel de luz que incide en la planta. | Lógico | TR-09, TR-31 | Sensores y procesamiento
LR-04 | Controlador del sistema | El sistema debe contener un controlador capaz de procesar la informacion de los sensores. | Lógico | TR-01, TR-02, TR-29, TR-05 | Control y Procesamiento
LR-05 | Actuador de sanida | El sistema debe contener un actuador para efectuar acciones de sonido. | Lógico | TR-12 | Sensores y procesamiento
LR-06 | Actuador de luz | El sistema debe contener un actuador para efectuar acciones de luz. | Lógico | TR-11 | Sensores y procesamiento
LR-07 | Interfaz de Usuario Gráfico | El sistema debe de proveer una Interfaz Grafica de Usuario (GUI) para interactuar con el usuario. | Lógico | TR-06, TR-20, TR-30 | GUI y config
LR-08 | Sensado de temperatura | El sistema debe medir periódicamente la temperatura del ambiente utilizando el sensor de temperatura. | Lógico | TR-02, TR-08, TR-17 | Control y Procesamiento
LR-09 | Sensado de humedad | El sistema debe medir periódicamente la humedad del suelo de la planta utilizando el sensor de humedad. | Lógico | TR-02, TR-10, TR-17, TR-32 | Control y Procesamiento
LR-10 | Sensado de nivel luz | El sistema debe medir periódicamente el nivel de luz que incide en la planta utilizando el sensor de luz. | Lógico | TR-02, TR-09, TR-17, TR-31 | Control y Procesamiento
LR-11 | Controlador de datos del sensor | El controllador debe recibir la información de los sensores para procesarla. | Lógico | TR-04, TR-05, TR-29 | Control y Procesamiento
LR-12 | Base de datos Interna | El sistema debe almacenar la informacion de los sensores localmente en una base de datos interna. | Lógico | TR-07, TR-34 | Control y Procesamiento
LR-13 | Mostrar información de planta | El controlador debe mandar la informacion del estado de la planta a la GUI. | Lógico | TR-23, TR-27 | GUI y config
LR-14 | Configuracion de umbral de Temperatura | El sistema debe permitir al usuario configurar el valor de umbral de temperatura. | Lógico | TR-26 | GUI y config
LR-15 | Configuración de umbral de humedad | El sistema debe permitir al usuario configurar el valor de umbral de humedad. | Lógico | TR-26 | GUI y config
LR-16 | Configuración volumen del actuador | El sistema debe permitir al usuario configurar el volumen del actuador sonoro. | Lógico | TR-28 | GUI y config
LR-17 | Configuración brille del actuador | El sistema debe permitir al usuario configurar el brillo del actuador de luz. | Lógico | TR-28 | GUI y config
LR-18 | Configuración frecuencia de medición | El sistema debe de permitir al usuario configurar la frecuencia de presentacion de la informacion de los sensores. | Lógico | TR-19, TR-26 | GUI y config
LR-19 | Configuración de umral de nivel de luz | El sistema debe permitir al usuario configurar el valor de umbral de nivel de luz. | Lógico | TR-26 | GUI y config
LR-20 | Señal de temperatura | El sensor de temperatura debe mandar la señal de temperatura al controlador con el itemFlow Sens_data. | Lógico | TR-02, TR-04, TR-08 | Flujos de Datos y Funciones
LR-21 | Señal de humedad | El sensor de humedad debe mandar la señal de humedad al controlador con el itemFlow Sens_data. | Lógico | TR-02, TR-04, TR-10, TR-32 | Flujos de Datos y Funciones
LR-22 | Señal de luz | El sensor de luz debe mandar la señal de nivel de luz con el itemFlow Sens_data. | Lógico | TR-02, TR-04, TR-09, TR-31 | Flujos de Datos y Funciones
LR-23 | Valores de configuracion del controlador | El controlador debe recibir el itemFlow config_values cuando un nuevo valor de configuracion es requerido. | Lógico | TR-01, TR-04, TR-06 | Flujos de Datos y Funciones
LR-24 | Solicitud de actuación de controlador | El controlador debe mandar el itemFlow Act_com para solicitar una acción de los actuadores. | Lógico | TR-01, TR-02, TR-04 | Flujos de Datos y Funciones
LR-25 | Mostrar informacion gráfica de planta | La GUI debe recibír los intemFlow sens_data y plnt_stat para mostrar la información al usuario. | Lógico | TR-06, TR-23, TR-30 | Flujos de Datos y Funciones
LR-26 | Función de procesamiento de sensor | El controlador debe recibir el itemFlow sens_data, procesar la información y mandar la señal mes_values. | Lógico | TR-02, TR-05, TR-18 | Control y Procesamiento
LR-27 | Función calcular estatus planta | El controlador debe recibír los intemFlow mes_values y config_values para calcular el estado de la planta. | Lógico | TR-01, TR-05, TR-29 | Flujos de Datos y Funciones
LR-28 | Mostrar valorns de configuración | La GUI debe mandar el itemFlow config_values al controlador cuando se establece un nuevo valor. | Lógico | TR-06, TR-26, TR-30 | Flujos de Datos y Funciones
LR-29 | Función calcular emocion del robot | El controlador debe recibír el itemFlow plnt_stat para calcular la emoción del robot y mandar las señales son_com y lig_com. | Lógico | TR-01, TR-29 | Flujos de Datos y Funciones
LR-30 | Estructura plnt_stat | El itemFlow plnt_stat debe estar compuesto de tres variables: temp_stat, moist_stat y light_stat. | Lógico | TR-01, TR-02 | Lógica de Emociones y Comandos
LR-31 | Temperatura ok | Cuando el itemFlow temp_sensor_data < max_temp y temp_sensor_data> min_temp, el controlador debe establecer temp_stat = ok. | Lógico | TR-05, TR-02, TR-18 | Lógica de Emociones y Comandos
LR-32 | Temperatura Alta | Cuando el itemFlow temp_sensor_data >max_temp, el controlador debe establecer temp_stat = high. | Lógico | TR-05, TR-02, TR-18 | Lógica de Emociones y Comandos
LR-33 | Temperatura baja | Cuando el itemFlow temp_sensor_data < min_temp, el controlador debe establecer temp_stat = low. | Lógico | TR-05, TR-02, TR-18 | Lógica de Emociones y Comandos
LR-34 | Humedad ok | Cuando el itemFlow moist_sensor_data < max_moist y moist_sensor_data > min_moist, el controlador debe establecer moist_stat = ok. | Lógico | TR-05, TR-02, TR-18 | Lógica de Emociones y Comandos
LR-35 | Humedad alta | Cuando moist_sensor_data > max_moist, el controlador debe establecer moist_stat = high. | Lógico | TR-05, TR-02, TR-18 | Lógica de Emociones y Comandos
LR-36 | Humedad baja | Cuando moist_sensor_data < min_moist, el controlador debe establecer moist_stat = low. | Lógico | TR-05, TR-02, TR-18 | Lógica de Emociones y Comandos
LR-37 | Sin humedad | Cuando moist_sensor_data == 0, el controlador debe establecer moist_stat = dead. | Lógico | TR-05, TR-02, TR-18 | Lógica de Emociones y Comandos
LR-38 | Luz ok | Cuando light_sensor_data < max_light AND light_sensor_data > min_light, el controlador debe establacer temp_stat = ok. | Lógico | TR-05, TR-02, TR-18 | Lógica de Emociones y Comandos
LR-39 | Luz alta | Cuando light_sensor_data > max_light, el controlador debe establecer light_stat = high. | Lógico | TR-05, TR-02, TR-18 | Lógica de Emociones y Comandos
LR-40 | Luz baja | Cuando light_sensor_data < max_light, el controlador debe establecer light_stat = low. | Lógico | TR-05, TR-02, TR-18 | Lógica de Emociones y Comandos
LR-41 | Estados principales del sistema | El sistema debe tener dos estados principales "encendido" y "apagado". | Lógico | TR-01, TR-29 | Lógica de Emociones y Comandos
LR-42 | Estado "encendido" | Mientras el sistema este en el estado "encendido" debe entrar en los estados "monitorear planta", "Monitorear plantas" y "Determinar emcion del robot". | Lógico | TR-01, TR-29 | Lógica de Emociones y Comandos
LR-43 | Estado de sistema actuar emoción | Cuando plnt_emo != ok, el sistema debe entrar en el estado "Actuar emocion". | Lógico | TR-01, TR-29 | Lógica de Emociones y Comandos
LR-44 | Estructura emocion del robot | El itemFlow robot_emo debe estar compuesto por tres variables: temp_emo, moist_emo, light_emo. | Lógico | TR-01, TR-29 | Lógica de Emociones y Comandos
LR-45 | Emocion temperatura ok | Cuando temp_stat == ok, el controlard debe establecer temp_emo = ok. | Lógico | TR-01, TR-29 | Lógica de Emociones y Comandos
LR-46 | Emoción temperatura caliente | Cuando temp_stat == high, el controlador debe establecer temp_emo = hot. | Lógico | TR-01, TR-29 | Lógica de Emociones y Comandos
LR-47 | Emoción temperatura fría | Cuando temp_stat == low, el controlador debe establecer temp_emo = cold. | Lógico | TR-01, TR-29 | Lógica de Emociones y Comandos
LR-48 | Emoción humedad ok | Cuando moist_stat == ok, el controlador deber establecer moist_emo = ok. | Lógico | TR-01, TR-29 | Lógica de Emociones y Comandos
LR-49 | Emoción humedad seco | Cuando moist_stat == low, el controlador deber establecer moist_emo = dry. | Lógico | TR-01, TR-29 | Lógica de Emociones y Comandos
LR-50 | Emoción humedad muerto | Cuando moist_stat == dead, el controlador deber establecer moist_emo = dead. | Lógico | TR-01, TR-29 | Lógica de Emociones y Comandos
LR-51 | Emoción luz ok | Cuando light_stat == ok, el controlador deber establecer light_emo = ok. | Lógico | TR-01, TR-29 | Lógica de Emociones y Comandos
LR-52 | Emoción luz cansado | Cuando light_stat == high, el controlador debe establecer light_emo = tired. | Lógico | TR-01, TR-29 | Lógica de Emociones y Comandos
LR-53 | Emoción luz triste | Cuando light_stat == low, el controlador debe establecer light_emo = tired. | Lógico | TR-01, TR-29 | Lógica de Emociones y Comandos
LR-54 | Estructura comando luz | El itemFlow led_command debe estar compuesto de tres variables: color, modeo, velocidad. | Lógico | TR-01, TR-04, TR-02, TR-05, TR-11, TR-12 | Lógica de Emociones y Comandos
LR-55 | Estructura comando sonido | El itemFlow sound_command debe estar compuesto de dos variables: tono y velocidad. | Lógico | TR-01, TR-04, TR-02, TR-05, TR-11, TR-12 | Lógica de Emociones y Comandos
LR-56 | Comando emoción muerto | Cuando mosit_emo == dead, el controlador debe establecer led_command = [red, still]. | Lógico | TR-01, TR-04, TR-02, TR-05, TR-11, TR-12 | Lógica de Emociones y Comandos
LR-57 | Comando emoción seco | Cuando mosit_emo == dry, el controlador debe establcer led_command = [yellow, blink] y sound_command = [high,high]. | Lógico | TR-01, TR-04, TR-02, TR-05, TR-11, TR-12 | Lógica de Emociones y Comandos
LR-58 | Comando emoción caliente | Cuando temp_emo == hot y moist_emo == ok, el controlador debe establecer led_command = [red, blink] y sound_command = [low,high]. | Lógico | TR-01, TR-04, TR-02, TR-05, TR-11, TR-12 | Lógica de Emociones y Comandos
LR-59 | Comando emoción trio | Cuando temp_emo == cold y moist_emo == ok, el controlador debe establecer led_command = [blue,blink] y sound_command = [low,high]. | Lógico | TR-01, TR-04, TR-02, TR-05, TR-11, TR-12 | Lógica de Emociones y Comandos
LR-60 | Comando emoción triste | Cuando light_emo == sad y temp_emo == ok y moist_emo == ok, el controlador debe establecer led_command = [purple,still] y sound_command = [low, low]. | Lógico | TR-01, TR-04, TR-02, TR-05, TR-11, TR-12 | Lógica de Emociones y Comandos
LR-61 | Comando emoción cansado | Cuando light_emo == tired y temp_emo == ok y moist_emo == ok, el controlador debe establecer led_command = [cyan,blink] y sound_command = [high,high]. | Lógico | TR-01, TR-04, TR-02, TR-05, TR-11, TR-12 | Lógica de Emociones y Comandos
LR-62 | Comando emoción feliz | Cuando light_emo == ok y temp_emo == ok y moist_emo == ok, el controlador debe establecer led_command = [green,still] | Lógico | TR-01, TR-04, TR-02, TR-05, TR-11, TR-12 | Lógica de Emociones y Comandos
LR-63 | Comando emoción advertencia luz | Cuando light_emo != ok, el controlador debe establecer led_command = [orange,still] | Lógico | TR-01, TR-04, TR-02, TR-05, TR-11, TR-12 | Lógica de Emociones y Comandos
LR-64 | Comando emoción advertencia temperatura | Cuando temp_emo != ok, el controlador debe establecer led_command = [orange,still] | Lógico | TR-01, TR-04, TR-02, TR-05, TR-11, TR-12 | Lógica de Emociones y Comandos
LR-65 | Comando emoción advertencia humedad | Cuando mosit_emo != ok, el controlador debe establecer led_command = [orange,still] | Lógico | TR-01, TR-11, TR-29, TR-04 | Lógica de Emociones y Comandos
LR-66 | Lógica de Selección de Consejos | El sistema debe mostrar los consejos de cuidado correspondientes al perfil de planta seleccionado actualmente en la configuración. | Lógico | TR-25, TR-26 | GUI y config
TR-01 | Controlador principal | El sistema utilizará un microprocesador Raspberry Pi Zero como unidad de control principal para tareas de alto nivel. | Tecnológico | LR-04, LR-11, LR-27, LR-29 | Control y Procesamiento
TR-02 | Microcontrolador de Entradas y Salidas | El sistema debe usar un microcontrolador Raspberry Pi Pico para la gestión de entradas y salidas. | Tecnológico | LR-04, LR-08 a LR-10, LR-26 | Control y Procesamiento
TR-03 | Voltajes de operacion | Los componentes del sistema deben operar a 5V y 3.3V. | Tecnológico | Refines todo los de Hardware | No Funcionales
TR-04 | Comuncacion de control | La comunicación entre la Pi Zero y la Pi Pico debe implementarse usando el protocolo serial UART. | Tecnológico | LR-11, LR-20 a LR-24 | Control y Procesamiento
TR-05 | Firmware del microcontrolador | El firmware de la Raspberry Pi Pico debe ser desarrollado en MicroPython. | Tecnológico | LR-04, LR-26, TR-33 | Control y Procesamiento
TR-06 | Servidor Web de Interfaz | La GUI debe ser servida por un servidor web local implementado con el micro-framework Flask. | Tecnológico | CR-10, LR-07, LR-25, LR-28 | GUI y config
TR-07 | Almacenamiento Base de Datos | El historial de datos de los sensores debe almacenarse en una base de datos local SQLite. | Tecnológico | CR-22, LR-12 | Almacenamiento y Procesamiento de Datos
TR-08 | Sensor de Temperatura | El sistema debe usar un sensor DHT11 para medir la temperatura ambiental. | Tecnológico | CR-02, LR-01, LR-08 | Sensores y procesamiento
TR-09 | Sensor de luz | El sistema debe usar un sensor BH1750 para medir la intensidad de luz ambiental. | Tecnológico | CR-03, LR-03, LR-10 | Sensores y procesamiento
TR-10 | Sensor de humedad | El sistema debe usar un sensor capacitivo OKY3443-1 para medir la humedad del suelo. | Tecnológico | CR-04, LR-02, LR-09 | Sensores y procesamiento
TR-11 | Actuador Visual | El sistema debe usar una tira de LEDs direccionables WS2812B para la retroalimentación visual. | Tecnológico | CR-09, CR-27, CR-29, CR-30 a CR-37, LR-06 | Alertas y actuadores
TR-12 | Actuador Auditivo | El sistema debe usar un Buzzer Pasivo controlado por PWM para la retroalimentación auditiva. | Tecnológico | CR-08, CR-27, CR-29, CR-31 a CR-35, LR-05 | Alertas y actuadores
TR-13 | Fabricacion de la carcaza | La carcaza y los encapsulamientos internos deben ser fabricados mediante Impresión 3D. | Tecnológico | CR-28 | No Funcionales
TR-14 | Material de fabricacion | El material de fabricacion debe ser Ácido Poliláctico (PLA). | Tecnológico | Refines: TR-13 | No Funcionales
TR-15 | Plataforma CAD | El diseño de la carcaza debe ser modelado en la plataforma "Onshape" y ser de acceso público. | Tecnológico | CR-28 | No Funcionales
TR-16 | Fuente de alimentacion | El sistema debe ser alimentado por una única fuente de alimentación centralizada de 5 Volts y 2 Ampers. | Tecnológico | TR-03 | No Funcionales
TR-17 | Frequencia de muestreo | El microcontrolador debe leer todos los sensores físicos con una frecuencia de 1 Segundo. | Tecnológico | LR-08, LR-09, LR-10 | Almacenamiento y Procesamiento de Datos
TR-18 | Filtrado de media movil | El sistema debe promediar los valores recibidos por los sensores y promediarlos despues de una cantidad especifica de mediciones antes de reportar el valor final. | Tecnológico | LR-26 | Almacenamiento y Procesamiento de Datos
TR-19 | Filtrado de señal | El sistema debe permitir la configuración de la cantidad de mediciones a promediar. | Tecnológico | CR-20, LR-18 | Almacenamiento y Procesamiento de Datos
TR-20 | Estructura GUI | La Interfaz Gráfica de Usuario debe estar estructurada en cuatro pantallas principales: Inicio, Estadísticas, Consejos y Configuración. | Tecnológico | LR-07 | GUI y config
TR-21 | Plantilla de GUI | La Interfaz Grafica de usuario debe usar una plamntilla para compartir la estructura entre pantallas. | Tecnológico | Refines TR-20 y TR-30 | GUI y config
TR-22 | Estructura de Plantilla | La estructura de la plantilla debe estar compuesta de botones para navegar por la interfaz, el nombre del robot y la pagina actual. | Tecnológico | Refines TR-21 | GUI y config
TR-23 | Pantalla de inicio | La pantalla de inicio debe de mostrar las mediciones actuales de los sensores, la estampa de tiempo de la ultima medicion, el estado actual del robot y el perfil seleccionado actualmente. | Tecnológico | CR-10, LR-13, LR-25 | GUI y config
TR-24 | Pantalla de estadisticas | La pantalla de estaisticas debe mostrar el registro de mediciones del robot para cada sensor. | Tecnológico | CR-22 | GUI y config
TR-25 | Pantalla de Consejos | La pantalla de consejos debe de presentar informacion relevante para el cuidado del perfil de planta seleccionado. | Tecnológico | CR-16, LR-66 | GUI y config
TR-26 | Pantalla de configuracion | La pantalla de configuracion debe mostrar un menu que permita al usuario cambiar las configuraciones del robot. | Tecnológico | CR-17, CR-21, LR-14, LR-15, LR-19 | GUI y config
TR-27 | Refresco de datos de GUI | Los datos de los sensores mostrados en la pantalla "Inicio" deben refrescarse automáticamente cada 3 segundos. | Tecnológico | CR-10, LR-13 | GUI y config
TR-28 | Configuracion de actuadores | La pantalla de configuracion debe permitir al usuario configurar la intesisdad de los actuadores de volumen y brillo. | Tecnológico | CR-18, CR-19, LR-16, LR-17 | GUI y config
TR-29 | Sistema Operativo del Controlador Principal | El microprocesador Raspberry Pi Zero debe utilizar el sistema operativo Raspberry Pi OS Lite, para gestionar los procesos de alto nivel, el servidor web y la base de datos. | Tecnológico | CR-05, LR-04, LR-29 | Control y Procesamiento
TR-30 | Tecnología de Frontend de GUI | La Interfaz Gráfica de Usuario debe ser renderizada utilizando tecnologías web estándar (HTML5, CSS3) y JavaScript para la interactividad de la GUI. | Tecnológico | LR-07 | GUI y config
TR-31 | Interfaz del Sensor de Luz | El sensor de luz BH1750 debe comunicarse con la Raspberry Pi Pico utilizando el protocolo de bus I2C. | Tecnológico | LR-03, LR-10 | Sensores y procesamiento
TR-32 | Interfaz del Sensor de Humedad | El sensor de humedad capacitivo debe ser leído a través de uno de los pines de Conversor Analógico-Digital de la Raspberry Pi Pico | Tecnológico | LR-02, LR-09 | Sensores y procesamiento
TR-33 | Autonomía del Microcontrolador | El firmware de la Raspberry Pi Pico debe ser capaz de operar de forma autónoma, ejecutando las funciones esenciales como el sensado y las alertas. | Tecnológico | CR-25, CR-26 | Control y Procesamiento
TR-34 | Esquema de Base de Datos | La base de datos SQLite debe contener una tabla de mediciones que almacene una marca de tiempo, el valor del sensor de temperatura, el valor del sensor de humedad y el valor del sensor de luz para su uso en la pantalla de estadísticas. | Tecnológico | CR-22, LR-12 | Almacenamiento y Procesamiento de Datos

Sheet: Hoja1
Sensores y Procesamiento
ID Conceptual (CR) | Nombre Conceptual | ID Lógico (LR) | Nombre Lógico | ID Tecnológico (TR) | Nombre Tecnológico
CR-01 | Monitoreo del ambiente | LR-01 | Sensor de temperatura | TR-08 | Sensor de Temperatura (DHT11)
 |  | LR-02 | Sensor de humedad | TR-10, TR-32 | Sensor de humedad (Capacitivo), Interfaz (ADC)
 |  | LR-03 | Sensor de luz | TR-09, TR-31 | Sensor de luz (BH1750), Protocolo (I2C)
CR-02 | Sensado de Temperatura | LR-01 | Sensor de temperatura | TR-08 | Sensor de Temperatura (DHT11)
 |  | LR-08 | Sensado de temperatura (periódico) | TR-02, TR-17 | Microcontrolador (Pico), Frecuencia (1s)
 |  | LR-31, 32, 33 | Lógica de estado (ok, alta, baja) | TR-05 | Firmware (MicroPython)
CR-03 | Sensado de nivel de luz | LR-03 | Sensor de luz | TR-09, TR-31 | Sensor de luz (BH1750), Protocolo (I2C)
 |  | LR-10 | Sensado de nivel luz (periódico) | TR-02, TR-17 | Microcontrolador (Pico), Frecuencia (1s)
 |  | LR-38, 39, 40 | Lógica de estado (ok, alta, baja) | TR-05 | Firmware (MicroPython)
CR-04 | Sensado de humedad | LR-02 | Sensor de humedad | TR-10, TR-32 | Sensor de humedad (Capacitivo), Interfaz (ADC)
 |  | LR-09 | Sensado de humedad (periódico) | TR-02, TR-17 | Microcontrolador (Pico), Frecuencia (1s)
 |  | LR-34, 35, 36 | Lógica de estado (ok, alta, baja) | TR-05 | Firmware (MicroPython)
CR-05 | Procesamiento | LR-04 | Controlador del sistema | TR-01, TR-02 | Controlador (Pi Zero), Microcontrolador (Pico)
 |  | LR-12 | Base de datos Interna | TR-07, TR-34 | Almacenamiento (SQLite), Esquema de BD
 |  | LR-26 | Función de procesamiento | TR-02, TR-18 | Microcontrolador (Pico), Filtrado (Media Móvil)
 |  | LR-27 | Función calcular estatus planta | TR-01, TR-29 | Controlador (Pi Zero), Sistema Operativo (OS Lite)
CR-06 | Umbrales criticos | LR-27 | Función calcular estatus planta | TR-01, TR-29 | Controlador (Pi Zero), Sistema Operativo (OS Lite)
 |  | LR-31 a LR-40 | Lógica de estado (Temp, Hum, Luz) | TR-05 | Firmware (MicroPython)
Alertas y Actuadores
ID Conceptual (CR) | Nombre Conceptual | ID Lógico (LR) | Nombre Lógico | ID Tecnológico (TR) | Nombre Tecnológico
CR-07 | Pedir ayuda | LR-29 | Función calcular emocion | TR-01, TR-29 | Controlador (Pi Zero), OS (Lite)
 |  | LR-47 a LR-53 | Lógica de Emoción (frío, seco, etc.) | TR-01, TR-29 | Controlador (Pi Zero), OS (Lite)
 |  | LR-56 a LR-62 | Lógica de Comando (color, sonido) | TR-11, TR-12, TR-04 | Actuador (LED), Actuador (Buzzer), Com. (UART)
CR-08 | Alerta sonora | LR-05 | Actuador de sonido | TR-12 | Actuador Auditivo (Buzzer)
 |  | LR-55 | Estructura comando sonido | TR-05 | Firmware (MicroPython)
CR-09 | Alerta visual | LR-06 | Actuador de luz | TR-11 | Actuador Visual (LED WS2812B)
 |  | LR-54 | Estructura comando luz | TR-05 | Firmware (MicroPython)
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

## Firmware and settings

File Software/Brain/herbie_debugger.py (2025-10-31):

# herbie_combined_app.py
import serial
import time
import json
import threading
from flask import Flask, render_template, request, redirect, url_for
import sys

# --- Configuración ---
AVR_WIN = 5       
SERIAL_PORT = '/dev/ttyS0'
BAUD_RATE = 9600

MIN_MOISTURE = 10.0   # % Humedad Suelo: Por debajo -> DRY
MAX_TEMP = 50.0       # °C Temperatura: Por encima -> HOT
MIN_TEMP = 15.0       # °C Temperatura: Por debajo -> COLD
MIN_LIGHT = 10.0     # Lux Luz: Por debajo -> SAD
MAX_LIGHT = 1000.0   # Lux Luz: Por encima -> TIRED

thresholds = {
    "MIN_MOISTURE": MIN_MOISTURE,
    "MAX_TEMP": MAX_TEMP,
    "MIN_TEMP": MIN_TEMP, 
    "MIN_LIGHT": MIN_LIGHT, 
    "MAX_LIGHT": MAX_LIGHT 
}

# --- Variables Globales ---
ser = None 
readings_buffer = [] 
latest_average_data = { # Inicializado con claves
    'timestamp': None, 'moisture': None, 'temperature': None, 
    'humidity': None, 'light': None
}
data_lock = threading.Lock()
new_average_calculated = False 
flag_lock = threading.Lock()
current_state_on_pico = None # Para recordar el último estado enviado
state_lock = threading.Lock() # Lock para esta nueva variable

# --- Lógica de Promediado ---
def calculate_and_update_average(buffer):
    """
    Calcula el promedio, determina el estado, envía el comando (si cambia) y 
    actualiza la variable global de datos.
    """
    
    global latest_average_data, data_lock

    # --- Cálculo de promedios ---
    valid_moisture = [r['moisture'] for r in buffer if r.get('moisture') is not None]
    valid_temp = [r['temperature'] for r in buffer if r.get('temperature') is not None]
    valid_humidity = [r['humidity'] for r in buffer if r.get('humidity') is not None]
    valid_light = [r['light'] for r in buffer if r.get('light') is not None]

    avg_moisture = round(sum(valid_moisture) / len(valid_moisture), 2) if valid_moisture else None
    avg_temp = round(sum(valid_temp) / len(valid_temp), 2) if valid_temp else None
    avg_humidity = round(sum(valid_humidity) / len(valid_humidity), 2) if valid_humidity else None
    avg_light = round(sum(valid_light) / len(valid_light), 2) if valid_light else None

    average_data_readings = {
        "moisture": avg_moisture, "temperature": avg_temp,
        "humidity": avg_humidity, "light": avg_light,
        "timestamp": time.strftime("%Y-%m-%d %H:%M:%S") 
    }

    print(f"DEBUG: avg_light = {avg_light}")

    # --- Lógica de Estado Automático ---
    current_state = determine_plant_state(avg_moisture, avg_temp, avg_light, thresholds)

    # --- Añade el estado al diccionario de datos ---
    average_data_to_display = average_data_readings.copy() # Copia los datos
    average_data_to_display["state"] = current_state

    with data_lock:
        latest_average_data = average_data_to_display # Guarda el diccionario con el estado

    with flag_lock:
        new_average_calculated = True

    print(f"--- Datos prtomediados ---")
    print(f"Estado: {current_state}")


# --- determinar estadod e la planta ---
def determine_plant_state(avg_moisture, avg_temp, avg_light, thresholds):
    """
    Determina el estado de la planta basado en las lecturas promedio y los umbrales.
    Sigue un orden de prioridad: Humedad > Temperatura > Luz.
    """
    
    # Prioridad 1: Humedad
    if avg_moisture is None or avg_moisture == 0:
        return "DEAD" # Sensor desconectado o completamente seco = muerto
    if avg_moisture < thresholds["MIN_MOISTURE"]:
        return "DRY"
        
    # Prioridad 2: Temperatura (solo si la humedad está bien)
    if avg_temp is not None: # Solo checar si tenemos lectura válida
        if avg_temp > thresholds["MAX_TEMP"]:
            return "HOT"
        if avg_temp < thresholds["MIN_TEMP"]:
            return "COLD"
            
    # Prioridad 3: Luz (solo si humedad y temperatura están bien)
    if avg_light is not None: # Solo checar si tenemos lectura válida
        if avg_light < thresholds["MIN_LIGHT"]:
            return "SAD" 
        if avg_light > thresholds["MAX_LIGHT"]:
            return "TIRED"
            
    # Si ninguna condición de "problema" se cumplió, todo está OK
    return "OK"


def send_state_command(state_name):
    """
    Envía un comando de estado a la Pico, SOLO si es diferente al último enviado.
    Actualiza el estado recordado.
    """
    global ser, current_state_on_pico, state_lock
    
    state_name = state_name.upper() # Asegura mayúsculas
    
    with state_lock: # Acceso seguro a la variable compartida
        # Comprueba si el estado es NUEVO
        if state_name != current_state_on_pico:
            command_json = f'{{"command": "set_state", "type": "{state_name}"}}\n'
            try:
                if ser:
                    print(" ")
                    print(f"H.E.R.B.I.E. state: {state_name}")
                    ser.write(command_json.encode('utf-8'))
                    current_state_on_pico = state_name # Actualiza el estado recordado SÓLO si se envió
                else:
                     print("⚠️ No se pudo enviar comando: Puerto serie no disponible.")
            except Exception as e:
                print(f"Error al escribir en el puerto serie: {e}")
        # else: # Opcional: imprimir si el estado no cambió
            # print(f"ℹ️ Estado ya es {state_name}, no se envía comando.")

# --- Hilo de Escucha Serial (Modificado) ---
def serial_listener_loop():
    global ser, readings_buffer
    print("Hilo Lector: Iniciando...")
    # No ponemos el delay aquí, lo controla el main

    while True:
        line_processed = False # Bandera para saber si hicimos algo
        try:
            # Intenta leer solo si hay datos, sin bloquear mucho tiempo
            if ser and ser.in_waiting > 0:
                line_bytes = ser.readline()
                if line_bytes:
                    line_processed = True # Marcamos que leímos algo
                    json_string = line_bytes.decode('utf-8', errors='ignore').strip()
                    if json_string and json_string.startswith('{') and json_string.endswith('}'):
                        try:
                            data = json.loads(json_string)
                            readings_buffer.append(data)
                            buffer_count = len(readings_buffer)
                            print(f"Lectura Recibida ({buffer_count}/{AVR_WIN})") 

                            if buffer_count >= AVR_WIN:
                                calculate_and_update_average(readings_buffer)
                                readings_buffer.clear()
                                
                        except json.JSONDecodeError:
                            print(f"‼️ Hilo Lector: Error JSON: {json_string}")
                    elif json_string:
                         print(f"‼️ Hilo Lector: Recibido no-JSON: {json_string}")

        except serial.SerialException as e:
            print(f"Hilo Lector: Error Serial Grave: {e}")
            time.sleep(5) 
        except Exception as e:
            print(f"Hilo Lector: Error Inesperado: {e}")
            time.sleep(1)

        # Si no procesamos nada, dormimos un poco más para ceder CPU
        if not line_processed:
            time.sleep(0.1) 
        else:
             time.sleep(0.01) # Si leímos, dormimos muy poco

# --- Aplicación Web Flask (Sin cambios) ---
app = Flask(__name__)

def get_latest_average_from_memory():
    global latest_average_data, data_lock
    with data_lock:
        return latest_average_data.copy()

@app.route('/')
def index():
    """Muestra el dashboard. Solo imprime si hay datos nuevos"""
    global new_average_calculated, flag_lock, thresholds
    current_average_data = get_latest_average_from_memory()
    should_print_message = False # Variable local para decidir si imprimir
    with flag_lock:
        if new_average_calculated:
            should_print_message = True
            new_average_calculated = False

    # Imprime el mensaje SOLO si la bandera estaba activa
    if should_print_message:
        print(f"Datos: {current_average_data}")

    return render_template('debugger.html', data=current_average_data, thresholds=thresholds)

@app.route('/send_command', methods=['POST'])
def handle_command():
    """Ruta para recibir el comando manual del dropdown."""
    if request.method == 'POST':
        selected_emotion = request.form.get('emotion') # Usar .get() es más seguro
        if selected_emotion: # Asegura que no esté vacío
            send_state_command(selected_emotion) # Llama a la función centralizada
    return redirect(url_for('index')) # Redirige de vuelta a la página principal



# --- Inicio del Programa ---
if __name__ == '__main__':
    # 1. Intenta abrir el puerto serie
    try:
        ser = serial.Serial(SERIAL_PORT, BAUD_RATE, timeout=0.1) # Timeout más corto
        ser.flush()
        print("Puerto serie conectado.")
    except serial.SerialException as e:
        print(f"Error fatal abriendo puerto serie {SERIAL_PORT}: {e}")
        exit()

    # 2. Inicia el hilo de escucha serial (que calcula promedios y envía estados automáticos)
    listener_thread = threading.Thread(target=serial_listener_loop, daemon=True)
    listener_thread.start()

    # 3. Envía el comando STARTUP a la Pico
    send_state_command("STARTUP")

    # 3. Inicia el servidor web Flask (que recibe comandos manuales de la GUI)
    print(f"Iniciando servidor web en http://0.0.0.0:5000")
    try:
        # debug=False es más seguro, threaded=True puede ayudar con hilos
        app.run(host='0.0.0.0', port=5000, debug=False, threaded=True)
    except KeyboardInterrupt:
        print("\nCerrando servidor web...")
    finally:
        send_state_command("SHUTDOWN")
        time.sleep(1)
        
        if ser and ser.is_open:
            ser.close()
            print("Puerto serie cerrado.")

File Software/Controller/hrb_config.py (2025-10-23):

# hrb_config.py

from machine import Pin, ADC, UART

# --- Pins ---
# Sensors
temp_pin = 16
moist_pin = 26
i2c_scl_pin = 8
i2c_sda_pin = 9
# Actuators
buzzer_pin = 14
led_data_pin = 18


# --- Constants ---
init_delay = 2 # initial sensor warm-up time
sleep_interval = 1 # interval between reads
led_count = 8 # actuator leds

# --- Calibration values ---
val_dry = 53437  # Value obtained with the sensor dry
val_mois = 40105 # Value obtained with the sensor in water

# --- Hardware ---
uart = UART(0, baudrate=9600, tx=Pin(0), rx=Pin(1))

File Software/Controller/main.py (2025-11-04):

# main.py (Pico)
import time
import ujson

import hrb_config as config
import hrb_sensors as sensors
import hrb_communication as communication
import hrb_actuators as actuators

def process_command(command_line):
    """
    Process command from Pi Zero
    """
    try:
        data = ujson.loads(command_line)
        print(f"Command: {data}")
        
        command = data.get("command")

        if command == "set_state":
            state_type = data.get("type") # Ej: "DRY", "HOT", etc.
            if state_type in actuators.state_map:
                actuators.state_map[state_type]()  
            else:
                print(f"ERROR: State '{state_type}' not defined.")
        
        
        elif command == "set_volume":
            level = data.get("value") # Float de 0.0 a 1.0
            if level is not None:
                actuators.update_volume(level)
                
        elif command == "set_brightness":
            level = data.get("value") # Float de 0.0 a 1.0
            if level is not None:
                actuators.update_brightness(level)
                
    except (ValueError, TypeError):
        print(f"ERROR: JSON command not recognized: {command_line}")

def main():
    print("Start HERBIE...")
    time.sleep(config.init_delay)
    
    sensors.init_sensors()
    actuators.init_actuators()
    
    try:
        
        while True:
            moist_data = sensors.get_moist()
            temp_data, humid_data = sensors.get_temp()
            light_data = sensors.get_light()

            if moist_data is None: moist_data = 0.0
            
            communication.send_data(moist_data, temp_data, humid_data, light_data)
            
            if config.uart.any():
                command_line = config.uart.readline()
                if command_line:
                    process_command(command_line)
            
            time.sleep(config.sleep_interval)
            
    except KeyboardInterrupt:
        print("\nUser stop.")
    finally:
        print("System shutdown...")
        # actuators.run_state_shutdown() # Opcional, ya que la Zero lo llama

if __name__ == "__main__":
    main()

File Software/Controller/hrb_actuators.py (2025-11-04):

# hrb_actuators.py
import machine
import utime
import hrb_config
from ws2812 import WS2812

# --- Configuration Values ---
buzzer_pwm = None
VOLUME = 32768  # 50% by default
BRIGHTNESS = 0.5 # 50% by default

# --- Colors ---
BLACK = [0, 0, 0]
BLACK = [0, 0, 0]
RED, YELLOW, BLUE, ORANGE, MAGENTA, CYAN, GREEN = [BLACK]*7

# --- Config values update ---
def update_volume(level):
    """Updates global volume (0.0 a 1.0)"""
    global VOLUME
    
    VOLUME = int(level * 65535)
    print(f"Volume updated: {level} ({VOLUME})")

def update_brightness(level):
    """Updates flobal brightness and recalculates color"""
    global BRIGHTNESS, RED, YELLOW, BLUE, ORANGE, MAGENTA, CYAN, GREEN
    
    BRIGHTNESS = max(0.0, min(1.0, level)) 
    
    RED = [int(255 * BRIGHTNESS), 0, 0]
    YELLOW = [int(255 * BRIGHTNESS), int(150 * BRIGHTNESS), 0]
    BLUE = [0, 0, int(255 * BRIGHTNESS)]
    ORANGE = [int(255 * BRIGHTNESS), int(60 * BRIGHTNESS), 0]
    MAGENTA = [int(255 * BRIGHTNESS), 0, int(255 * BRIGHTNESS)]
    CYAN = [0, int(255 * BRIGHTNESS), int(255 * BRIGHTNESS)]
    GREEN = [0, int(255 * BRIGHTNESS), 0]
    print(f"Brillo actualizado a {level}")

# --- Initialization ---
def init_actuators():
    """Actuators initialization"""
    global buzzer_pwm, strip
    # Init Buzzer
    try:
        buzzer_pwm = machine.PWM(machine.Pin(hrb_config.buzzer_pin))
        buzzer_pwm.duty_u16(0) # Buzzer off
    except Exception as e:
        print(f"ERROR initializating buzzer: {e}")
    
    # Init NeoPixel
    try:
        strip = WS2812(machine.Pin(hrb_config.led_data_pin), hrb_config.led_count)
        led_turn_off() # Leds off
    except Exception as e:
        print(f"Error initializating NeoPixel: {e}")

    update_brightness(BRIGHTNESS)
    led_turn_off() # Leds off

# --- Hard Stop function
def off():
    """Emergency function for Hard stop"""
    print("Actuators off...")
    actuators.no_tone()
    actuators.led_turn_off()

# --- Sound primitives ---

def set_tone(frequency):
    """Activate buzzer to a specific freq"""
    if buzzer_pwm and frequency > 0:
        buzzer_pwm.freq(frequency)
        buzzer_pwm.duty_u16(VOLUME)
    elif buzzer_pwm:
        buzzer_pwm.duty_u16(0) # Freq 0 is off

def no_tone():
    """Buzzer off"""
    if buzzer_pwm:
        buzzer_pwm.duty_u16(0)

def beep(frequency, duration_ms):
    """Generate a beep"""
    set_tone(frequency)
    utime.sleep_ms(duration_ms)
    no_tone()

def pause(duration_ms):
    """No tone"""
    no_tone()
    utime.sleep_ms(duration_ms)

def sweep(start_freq, end_freq, duration_ms, steps=20):
    """Generate a sweep"""
    if not buzzer_pwm: return
    step_duration = duration_ms // steps
    freq_step = (end_freq - start_freq) / steps
    set_tone(start_freq)
    for i in range(steps):
        current_freq = start_freq + (freq_step * i)
        buzzer_pwm.freq(int(current_freq))
        utime.sleep_ms(step_duration)
    no_tone()

def vibrato(base_freq, offset, cycle_ms, total_duration_ms):
    """Generate a vibrato"""
    if not buzzer_pwm: return
    end_time = utime.ticks_add(utime.ticks_ms(), total_duration_ms)
    while utime.ticks_diff(end_time, utime.ticks_ms()) > 0:
        set_tone(base_freq + offset); utime.sleep_ms(cycle_ms)
        if utime.ticks_diff(end_time, utime.ticks_ms()) <= 0: break
        set_tone(base_freq - offset); utime.sleep_ms(cycle_ms)
    no_tone()

# --- LED Primitives ---

def led_fill(color):
    """Fill strip of a color"""
    if strip:
        for i in range(hrb_config.led_count):
            strip[i] = color
        strip.write()

def led_turn_off():
    """LEDs off"""
    led_fill(BLACK)

def led_startup():
    """Startup sequence"""
    if not strip: return
    for i in range(hrb_config.led_count):
        strip[i] = GREEN
        strip.write()
        utime.sleep_ms(60)

def led_shutdown():
    """Shutdown sequence"""
    if not strip: return
    for i in range(hrb_config.led_count - 1, -1, -1):
        strip[i] = BLACK
        strip.write()
        utime.sleep_ms(60)

def led_shiver(color, cycle_ms, total_duration_ms):
    """
    Blink LEDs altrenated
    """
    if not strip: return
    
    end_time = utime.ticks_add(utime.ticks_ms(), total_duration_ms)
    
    while utime.ticks_diff(end_time, utime.ticks_ms()) > 0:
        
        for i in range(hrb_config.led_count):
            strip[i] = color if i % 2 == 0 else BLACK
        strip.write()
        utime.sleep_ms(cycle_ms)
        
        if utime.ticks_diff(end_time, utime.ticks_ms()) <= 0: break
            
        for i in range(hrb_config.led_count):
            strip[i] = color if i % 2 == 1 else BLACK
        strip.write()
        utime.sleep_ms(cycle_ms)
        
    led_turn_off()

# --- Emotion Functions (Sound and LED) ---

def run_state_dead():
    """EMOTION: DEAD - Red LED still, no sound"""
    print("EMOTION: DEAD")
    no_tone()
    led_fill(RED)
    
def run_state_dry():
    """EMOTION: DRY  - Yellow LED blink slow, low beeping sound"""
    print("EMOTION: DRY")
    for _ in range(3):
        set_tone(1200)
        led_fill(YELLOW)
        utime.sleep_ms(150)
        
        no_tone()
        led_turn_off()
        utime.sleep_ms(50)
        
        set_tone(800)
        led_fill(YELLOW)
        utime.sleep_ms(300)
        
        no_tone()
        led_turn_off()
        utime.sleep_ms(400)
        
    run_state_warning()

def run_state_hot():
    """EMOTION: HOT - Red LED blink slow, low to up sweep and beep"""
    print("EMOTION: HOT")
    
    led_fill(RED)
    sweep(800, 1600, 400)
    led_turn_off()
    pause(100)
    
    set_tone(1500)
    led_fill(RED)
    utime.sleep_ms(200)
    
    no_tone()
    led_turn_off()
    utime.sleep_ms(100)

    set_tone(1500)
    led_fill(RED)
    utime.sleep_ms(200)
    no_tone()
    led_turn_off()
    
    run_state_warning()

def run_state_cold():
    """EMOTION: COLD - Blue LED blinking fast, vibrato low"""
    print("EMOTION: COLD")
    beep(800,100)
    led_shiver(BLUE, 50, 200)
    pause(200)
    vibrato(1000, 100, 70, 400)
    led_shiver(BLUE, 70, 400)
    pause(200)
    vibrato(1000, 100, 70, 400)
    led_shiver(BLUE, 70, 400)
    led_turn_off()
    
    run_state_warning()
    
def run_state_sad():
    """EMOTION: SAD - Magenta LED blinking slow, low beep and sweep low to up."""
    print("EMOTION: SAD")
    for _ in range (2):
        led_fill(MAGENTA)
        beep(800,300)
        sweep(800,1000,100)
        
        led_turn_off() 
        pause(500)
        
    run_state_warning()

def run_state_tired():
    """EMOTION: TIRED - Cyan LED blinking fast, high beep blink"""
    print("EMOTION: TIRED")
    for _ in range(2):
        for _ in range(5):
            led_fill(CYAN)
            set_tone(1200)
            utime.sleep_ms(80)
            no_tone()
            led_turn_off()
            utime.sleep_ms(50)
        pause(120)
        
    run_state_warning()
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

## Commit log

2025-10-15 Added Circuits
    [Sesnsores.fzz, control.fzz]
2025-10-23 Added actuator module
2025-10-27 Added Actuator functions
2025-10-30 set color function sensors
2025-11-24 Mayor Changes in the architecture
    [ReqFull.xlsx, Reqs.xlsx, Sesnsores.fzz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]

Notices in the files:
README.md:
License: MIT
